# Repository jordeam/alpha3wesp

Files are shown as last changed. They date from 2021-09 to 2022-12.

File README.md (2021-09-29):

# alpha3wesp
Triphase trigger angle control using ESP32

## Pin connection

| ESP32 GPIO | Function |
|---|---|
| 15 | 60Hz square oscilator output for debug |
| 16 | 40kHz output oscilator for TPs |
| 17 | Gate of SCR 1 (Q1) |
| 18 | Gate of SCR 3 (Q3) |
| 19 | Gate of SCR 5 (Q5) |
| 25 | Gate of SCR 4 (Q4) |
| 26 | Gate of SCR 6 (Q6) |
| 27 | Gate of SCR 2 (Q2) |
| 4  | Grid Synchronism input |
| 36 | Analog input for alpha trigger angle |

The device works in 50Hz or 60Hz automatically.

SCR power bridge has its positive cycle devices tagged as Q1, for phase a, Q3 for phase b, and Q5 for phase c. The negative cycle for phase a is SCR number 4 (Q4), for phase b is Q6 and for phase c is Q2. This produces a trigger sequence in order, from Q1 to Q6.

## Circuit Example

An example of usage can be seen in [circuit-1](doc/example-circuit-1.pdf). In that circuit, a triphase full-bridge (or two way) rectifier is shown. Note the numbering of thyristors Q1 to Q6, it is very important to match with the ESP32 outputs. Also, certify that phases A, B and C are in the right sequence. For simplification, only one Gate Driver block is show, but it needs to be one for each thyristor.

An input of voltage from 0 to 2.5V means o to 180 degrees of trigger for each SCR.

## TODO

- accept inputs from UART, SPI, I2C, CAN and pulse width
- implement reversion capability for AC three-phase controllers
- use two phase synchronism signals to detect phase sequence order automatically
- as always, improve docs...

## Thanks

To all free software developers, thank you!

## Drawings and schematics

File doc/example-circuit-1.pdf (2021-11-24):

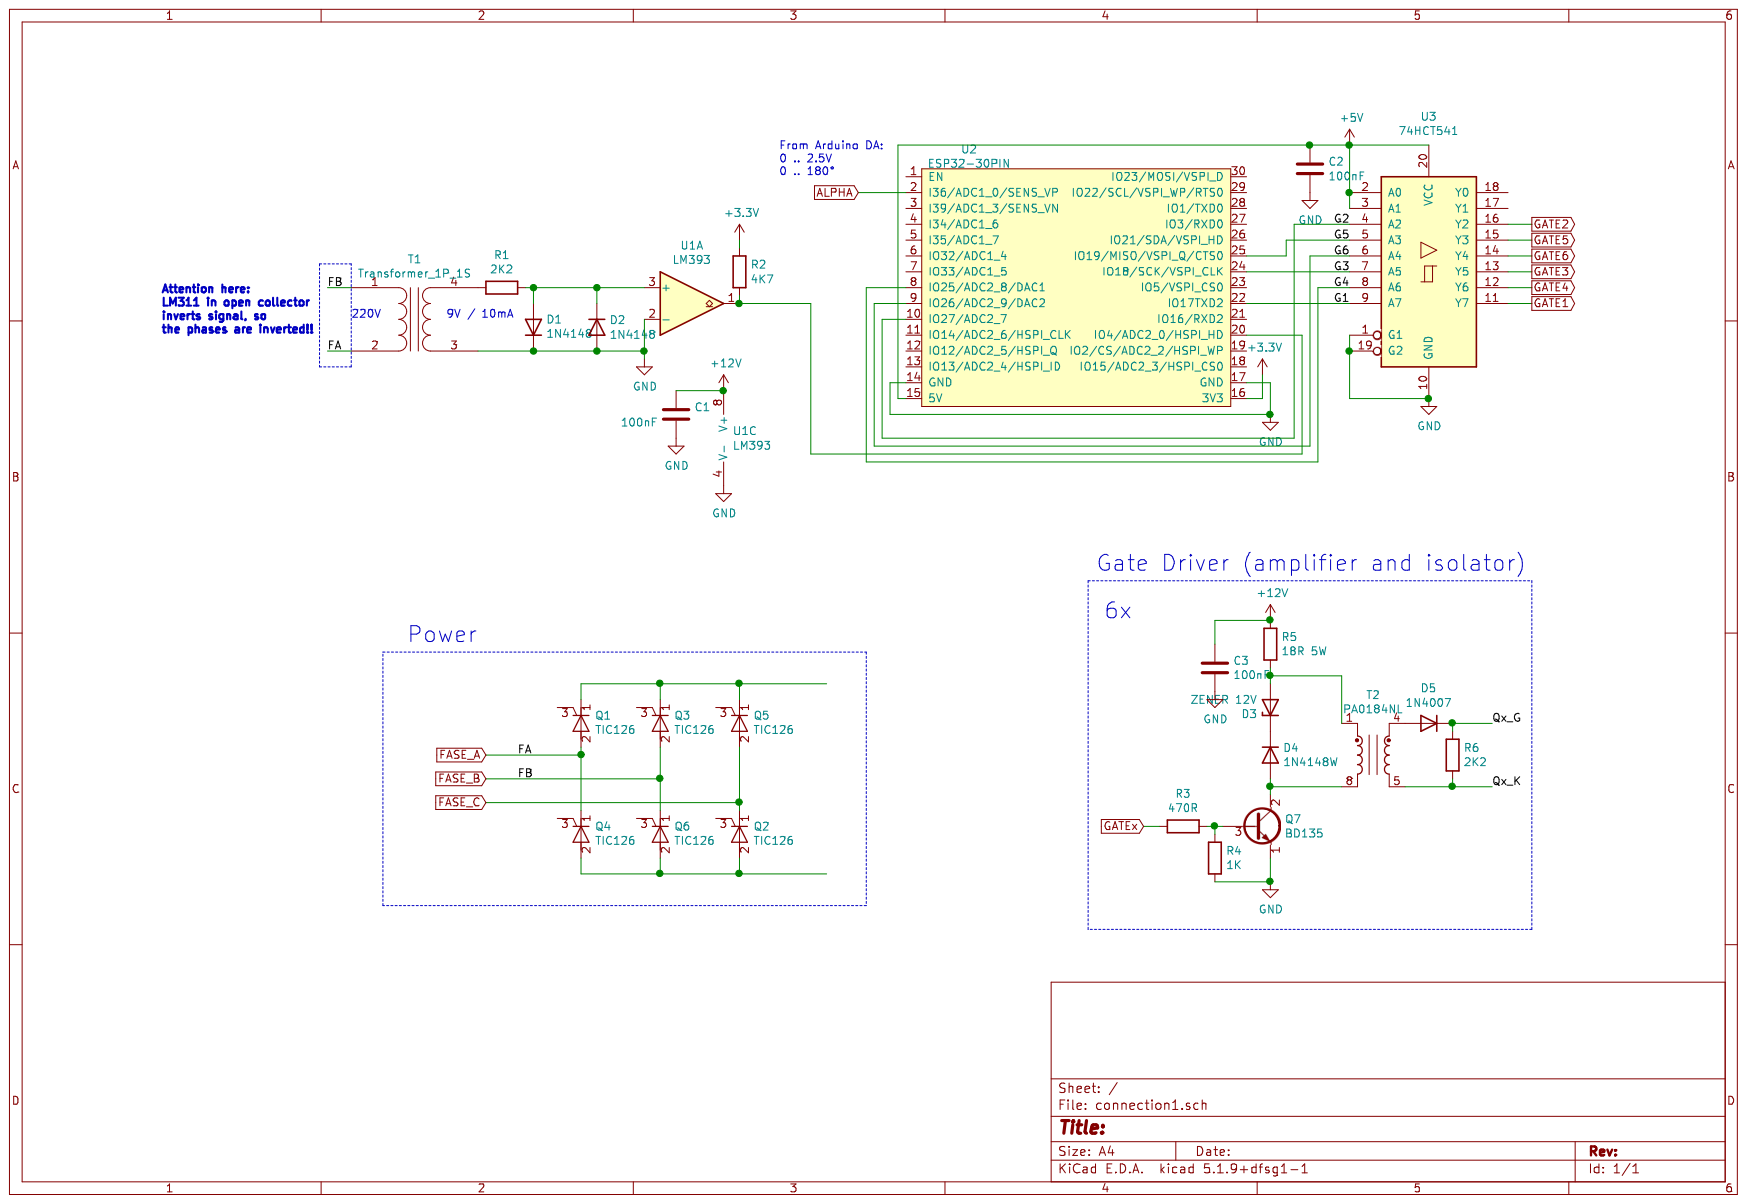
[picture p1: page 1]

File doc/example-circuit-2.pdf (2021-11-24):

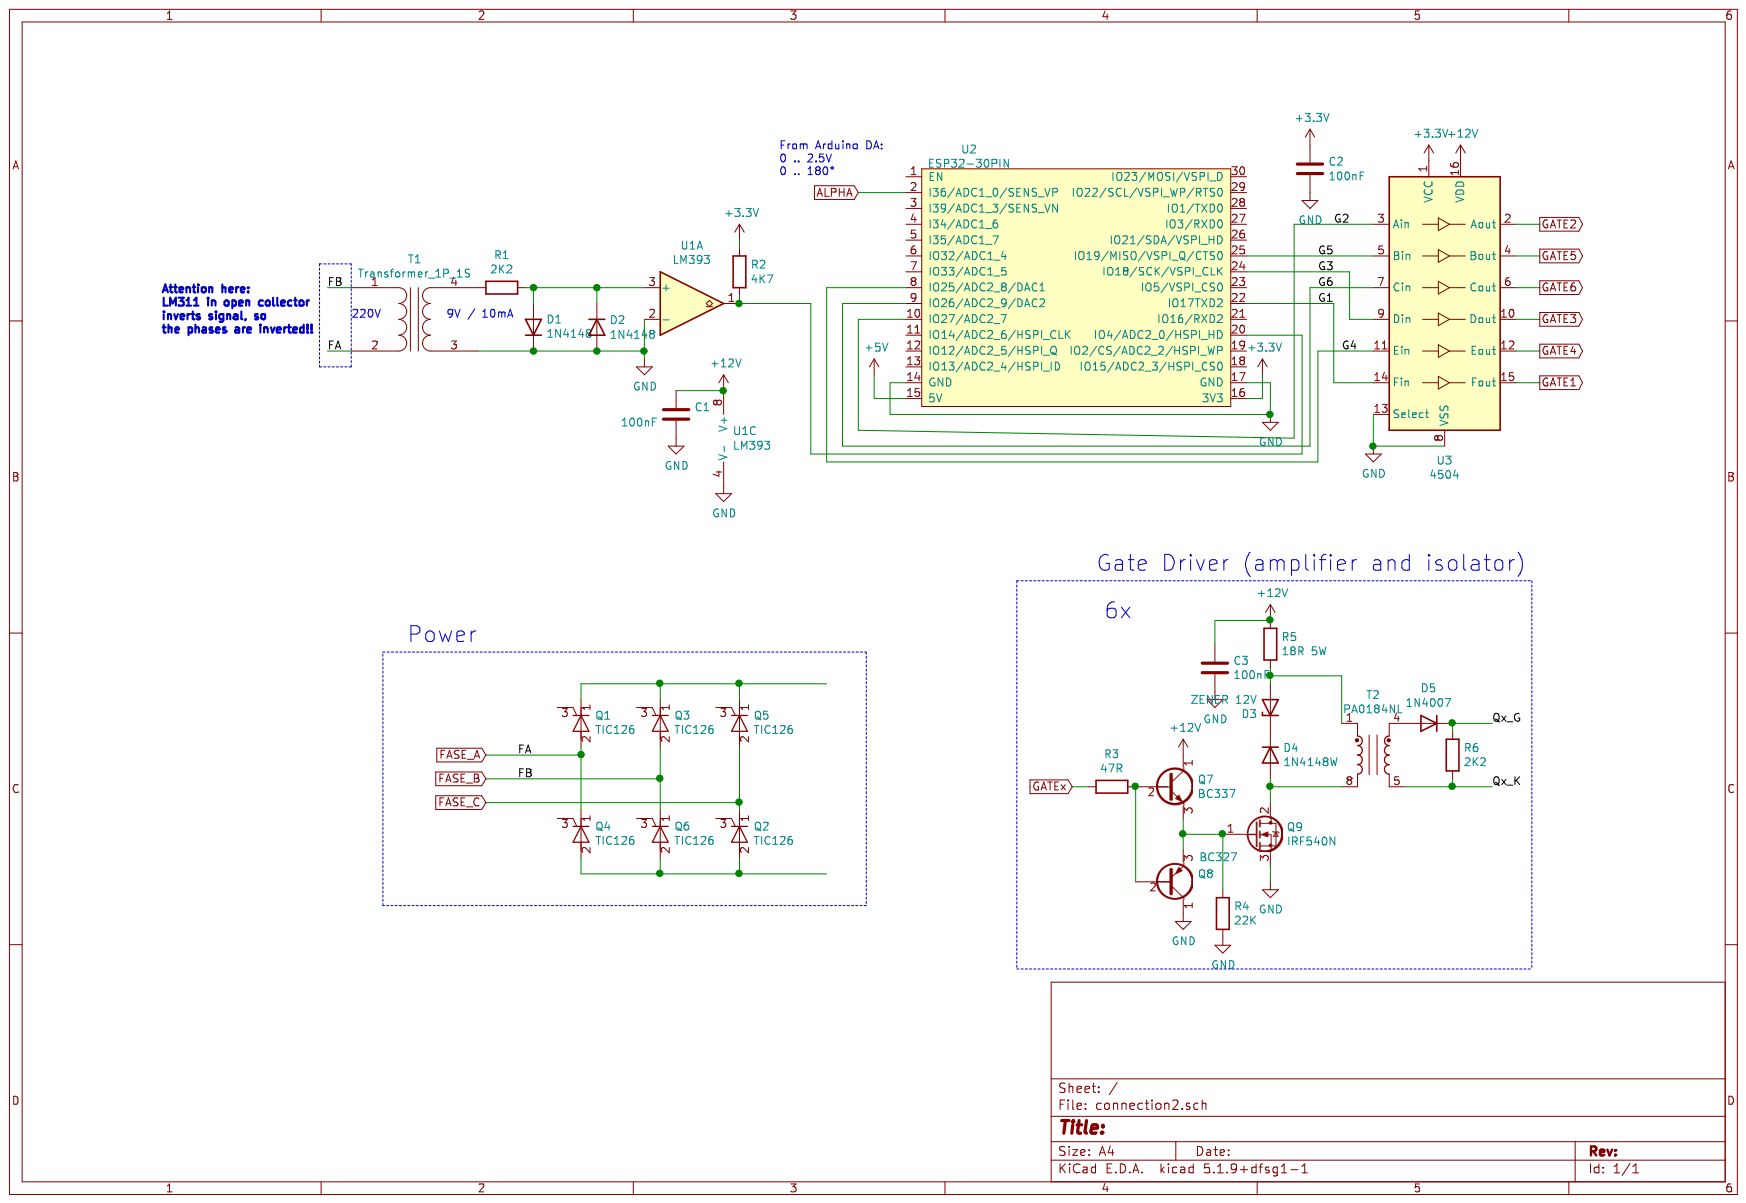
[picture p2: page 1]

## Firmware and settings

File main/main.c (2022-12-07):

#include <stddef.h>
#include <stdlib.h>
#include <stdint.h>
#include <string.h>

#include "freertos/FreeRTOS.h"
#include "freertos/task.h"
#include "freertos/queue.h"
#include "esp_intr_alloc.h"
#include "esp_attr.h"
#include "driver/timer.h"
#include "driver/gpio.h"
#include "driver/ledc.h"
#include "driver/adc.h"
#include "esp_adc_cal.h"

#include "pins.h"
#include "ledc_pwm.h"
#include "adc_mod.h"

#define GPIO_OUTPUT_PIN_SEL  (port_bit(LED_GPIO) | \
                              port_bit(SIGINT) | port_bit(SIGAD))

#define GPIO_INPUT_PIN_SEL  (port_bit(SYNC_GPIO) | port_bit(ADC_GPIO))

#define GATE_DUTY ((int)((1 << 10) * 0.4))

int sync;
int cnt, cnt_max = -1;
/* Maximum counter value used in last eval */
int cnt_max_e = 0;

/* the transitions */
struct tr {
  int rise[6], fall[6];
};

typedef struct tr tr_t;

tr_t gate;

static intr_handle_t s_timer_handle;
/* the alpha trigger angle in degrees */
float alpha = 60;

static void timer_isr(void* arg) {
  static int sync_old = 1;
  static tr_t g;

  gpio_set_level(SIGINT, 1);

  TIMERG0.int_clr_timers.t0 = 1;
  TIMERG0.hw_timer[0].config.alarm_en = 1;

  /* read SYNC */
  sync = gpio_get_level(SYNC_GPIO);

  if (sync && !sync_old && /* jitter ? */cnt > 20) {
    if (cnt_max < 0)
      cnt_max++;
    else if (cnt_max == 0)
      cnt_max = cnt;
    else {
      cnt_max += cnt;
      cnt_max >>= 1;
      memcpy(&g, &gate, sizeof(tr_t));

      /* Verify if Gates 4, 5 and 6 are higher than cnt */
      if (g.fall[3] >= cnt) {
        /* gpio_set_level(GATE4, 0); */
        ledc_set_duty(LEDC_HIGH_SPEED_MODE, LEDC_CHANNEL_4, 0);
        ledc_update_duty(LEDC_HIGH_SPEED_MODE, LEDC_CHANNEL_4);
      }
      if (g.fall[4] >= cnt) {
        /* gpio_set_level(GATE5, 0); */
        ledc_set_duty(LEDC_HIGH_SPEED_MODE, LEDC_CHANNEL_5, 0);
        ledc_update_duty(LEDC_HIGH_SPEED_MODE, LEDC_CHANNEL_5);
      }
      if (g.fall[5] >= cnt) {
        /* gpio_set_level(GATE6, 0); */
        ledc_set_duty(LEDC_HIGH_SPEED_MODE, LEDC_CHANNEL_6, 0);
        ledc_update_duty(LEDC_HIGH_SPEED_MODE, LEDC_CHANNEL_6);
      }
      if (g.rise[4] >= cnt) {
        /* gpio_set_level(GATE5, 1); */
        ledc_set_duty(LEDC_HIGH_SPEED_MODE, LEDC_CHANNEL_5, GATE_DUTY);
        ledc_update_duty(LEDC_HIGH_SPEED_MODE, LEDC_CHANNEL_5);
      }
      if (g.fall[3] >= cnt) {
        /* gpio_set_level(GATE4, 0); */
        ledc_set_duty(LEDC_HIGH_SPEED_MODE, LEDC_CHANNEL_4, 0);
        ledc_update_duty(LEDC_HIGH_SPEED_MODE, LEDC_CHANNEL_4);
      }
      if (g.rise[5] >= cnt) {
        /* gpio_set_level(GATE6, 1); */
        ledc_set_duty(LEDC_HIGH_SPEED_MODE, LEDC_CHANNEL_6, GATE_DUTY);
        ledc_update_duty(LEDC_HIGH_SPEED_MODE, LEDC_CHANNEL_6);
      }
    }
    cnt = 0;
  }

  /* do nothing if counter maximum is equal or less than zero*/
  if (cnt_max > 0) {
    /* refresh output pins */
    if (cnt == g.rise[0]) {
      /* gpio_set_level(GATE1, 1); */
      ledc_set_duty(LEDC_HIGH_SPEED_MODE, LEDC_CHANNEL_1, GATE_DUTY);
      ledc_update_duty(LEDC_HIGH_SPEED_MODE, LEDC_CHANNEL_1);
    }
    else if (cnt == g.fall[0]) {
      /* gpio_set_level(GATE1, 0); */
      ledc_set_duty(LEDC_HIGH_SPEED_MODE, LEDC_CHANNEL_1, 0);
      ledc_update_duty(LEDC_HIGH_SPEED_MODE, LEDC_CHANNEL_1);
    }
    if (cnt == g.rise[1]) {
      /* gpio_set_level(GATE2, 1); */
      ledc_set_duty(LEDC_HIGH_SPEED_MODE, LEDC_CHANNEL_2, GATE_DUTY);
      ledc_update_duty(LEDC_HIGH_SPEED_MODE, LEDC_CHANNEL_2);
    }
    else if (cnt == g.fall[1]) {
      /* gpio_set_level(GATE2, 0); */
      ledc_set_duty(LEDC_HIGH_SPEED_MODE, LEDC_CHANNEL_2, 0);
      ledc_update_duty(LEDC_HIGH_SPEED_MODE, LEDC_CHANNEL_2);
    }
    if (cnt == g.rise[2]) {
      /* gpio_set_level(GATE3, 1); */
      ledc_set_duty(LEDC_HIGH_SPEED_MODE, LEDC_CHANNEL_3, GATE_DUTY);
      ledc_update_duty(LEDC_HIGH_SPEED_MODE, LEDC_CHANNEL_3);
    }
    else if (cnt == g.fall[2]) {
      /* gpio_set_level(GATE3, 0); */
      ledc_set_duty(LEDC_HIGH_SPEED_MODE, LEDC_CHANNEL_3, 0);
      ledc_update_duty(LEDC_HIGH_SPEED_MODE, LEDC_CHANNEL_3);
    }
    if (cnt == g.rise[3]) {
      /* gpio_set_level(GATE4, 1); */
      ledc_set_duty(LEDC_HIGH_SPEED_MODE, LEDC_CHANNEL_4, GATE_DUTY);
      ledc_update_duty(LEDC_HIGH_SPEED_MODE, LEDC_CHANNEL_4);
    }
    else if (cnt == g.fall[3]) {
      /* gpio_set_level(GATE4, 0); */
      ledc_set_duty(LEDC_HIGH_SPEED_MODE, LEDC_CHANNEL_4, 0);
      ledc_update_duty(LEDC_HIGH_SPEED_MODE, LEDC_CHANNEL_4);
    }
    if (cnt == g.rise[4]) {
      /* gpio_set_level(GATE5, 1); */
      ledc_set_duty(LEDC_HIGH_SPEED_MODE, LEDC_CHANNEL_5, GATE_DUTY);
      ledc_update_duty(LEDC_HIGH_SPEED_MODE, LEDC_CHANNEL_5);
    }
    else if (cnt == g.fall[4]) {
      /* gpio_set_level(GATE5, 0); */
      ledc_set_duty(LEDC_HIGH_SPEED_MODE, LEDC_CHANNEL_5, 0);
      ledc_update_duty(LEDC_HIGH_SPEED_MODE, LEDC_CHANNEL_5);
    }
    if (cnt == g.rise[5]) {
      /* gpio_set_level(GATE6, 1); */
      ledc_set_duty(LEDC_HIGH_SPEED_MODE, LEDC_CHANNEL_6, GATE_DUTY);
      ledc_update_duty(LEDC_HIGH_SPEED_MODE, LEDC_CHANNEL_6);
    }
    else if (cnt == g.fall[5]) {
      /* gpio_set_level(GATE6, 0); */
      ledc_set_duty(LEDC_HIGH_SPEED_MODE, LEDC_CHANNEL_6, 0);
      ledc_update_duty(LEDC_HIGH_SPEED_MODE, LEDC_CHANNEL_6);
    }
  }

  /* increment counter */
  cnt++;
  /* refresh sync_old */
  sync_old = sync;
  /* flag interrupt exiting */
  gpio_set_level(SIGINT, 0);
}

void init_timer(int timer_period_us)
{
  timer_config_t timer_config = {
    .alarm_en = true,
    .counter_en = false,
    .intr_type = TIMER_INTR_LEVEL,
    .counter_dir = TIMER_COUNT_UP,
    .auto_reload = true,
    .divider = 80   /* 1 us per tick */
  };

  timer_init(TIMER_GROUP_0, TIMER_0, &timer_config);
  timer_set_counter_value(TIMER_GROUP_0, TIMER_0, 0);
  timer_set_alarm_value(TIMER_GROUP_0, TIMER_0, timer_period_us);
  timer_enable_intr(TIMER_GROUP_0, TIMER_0);
  timer_isr_register(TIMER_GROUP_0, TIMER_0, &timer_isr, NULL, 0, &s_timer_handle);

  timer_start(TIMER_GROUP_0, TIMER_0);
}

/* task to eval all trigger event times */
void eval_triggers(void * pvParams) {
  for (;;) {
    gpio_set_level(SIGAD, 1);
    int val = adc1_get_raw(ADC1_CHANNEL_0);
    gpio_set_level(SIGAD, 0);

    alpha = 180.0f * val / (1 << 12);
    cnt_max_e = cnt_max;
    /* verify if it detected the first sync pulse */
    if (cnt_max_e != 0) {
      if (alpha > 180.0f)
        alpha = 180.0f;
      float alpha_n = alpha / 360.0;
      gate.rise[0] = cnt_max_e * alpha_n;
      gate.fall[0] = cnt_max_e * 0.5;
      gate.rise[1] = cnt_max_e * (alpha_n + 0.1666);
      gate.fall[1] = cnt_max_e * 0.6666;
      gate.rise[2] = cnt_max_e * (alpha_n + 0.3333);
      gate.fall[2] = cnt_max_e * 0.8333;
      gate.rise[3] = cnt_max_e * (alpha_n + 0.5);
      gate.fall[3] = cnt_max_e - 1;
      gate.rise[4] = cnt_max_e * (alpha_n + 0.6666);
      if (gate.rise[4] >= cnt_max_e)
        gate.rise[4] -= cnt_max_e;
      gate.fall[4] = cnt_max_e * 0.1666;
      gate.rise[5] = cnt_max_e * (alpha_n + 0.8333);
      if (gate.rise[5] >= cnt_max_e)
        gate.rise[5] -= cnt_max_e;
      gate.fall[5] = cnt_max_e * 0.3333;
    }

    /* wait for something ? */
    vTaskDelay(pdMS_TO_TICKS(20));
  }
}

void led_task(void * pvParams) {
  for (int cnt = 0;;cnt = !cnt) {
    vTaskDelay(pdMS_TO_TICKS(200));
    gpio_set_level(LED_GPIO, cnt % 2);
  }
}

void app_main()
{
  /* init GPIOs */
  gpio_config_t io_conf_o = {
    .intr_type = GPIO_INTR_DISABLE,
    .mode = GPIO_MODE_OUTPUT,
    .pin_bit_mask = GPIO_OUTPUT_PIN_SEL,
    .pull_down_en = 0,
    .pull_up_en = 0
  };
  //configure GPIO with the given settings
  gpio_config(&io_conf_o);

  gpio_config_t io_conf_i = {
    .intr_type = GPIO_INTR_DISABLE,
    .pin_bit_mask = GPIO_INPUT_PIN_SEL,
    .mode = GPIO_MODE_INPUT,
    .pull_up_en = 0,
    .pull_down_en = 0,
  };
  gpio_config(&io_conf_i);

  /* configure LED PWMs */
  ledc_pwm_config();

  /* configure ADC raw */
  adc_config();

  /* register 50us interrupt SR */
  init_timer(50);

  /* TODO: clear this */
  /* alpha for test purposes */

  xTaskCreate(led_task, "led_task", 4096, NULL, 5, NULL);
  xTaskCreate(eval_triggers, "eval_triggers", 4096, NULL, 4, NULL);
}

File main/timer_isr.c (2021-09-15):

#include <stddef.h>
#include <stdlib.h>
#include <stdint.h>
#include "freertos/FreeRTOS.h"
#include "freertos/task.h"
#include "freertos/queue.h"
#include "esp_intr_alloc.h"
#include "esp_attr.h"
#include "driver/timer.h"
#include "driver/gpio.h"

/* Outputs:
   GPIO2: internal LED
   GPIO16: Oscilator 40kHz,
   GPIO17, 18, 19: positive semicycle phases 1, 2 and 3,
   GPIO25, 26, 27: negative senicycle phases 1, 2 and 3 */
#define GPIO_OUTPUT_PIN_SEL  ((1ULL<<2) | (1ULL<<16) | (1ULL<<17) | (1ULL<<18) | (1ULL<<19) | (1ULL<<25) | (1ULL<<26) | (1ULL<<27))

/* Inputs:
   GPIO4: sync
   GPIO34: ADC input angle
 */
#define GPIO_INPUT_PIN_SEL  ((1ULL<<4) | (1ULL<<34))

int sync;
uint32_t cnt, cnt_max = 0;
static intr_handle_t s_timer_handle;

static void timer_isr(void* arg)
{
  static int sync_old = 1;
  TIMERG0.int_clr_timers.t0 = 1;
  TIMERG0.hw_timer[0].config.alarm_en = 1;

  /* read SYNC */
  sync = gpio_get_level(4);

  if (sync && !sync_old) {
    cnt_max = cnt;
    cnt = 0;
  }
  else
    cnt++;
  sync_old = sync;

  /* eval outputs */
  /* refresh output pins */
}

void init_timer(int timer_period_us)
{
  timer_config_t config = {
    .alarm_en = true,
    .counter_en = false,
    .intr_type = TIMER_INTR_LEVEL,
    .counter_dir = TIMER_COUNT_UP,
    .auto_reload = true,
    .divider = 80   /* 1 us per tick */
  };

  timer_init(TIMER_GROUP_0, TIMER_0, &config);
  timer_set_counter_value(TIMER_GROUP_0, TIMER_0, 0);
  timer_set_alarm_value(TIMER_GROUP_0, TIMER_0, timer_period_us);
  timer_enable_intr(TIMER_GROUP_0, TIMER_0);
  timer_isr_register(TIMER_GROUP_0, TIMER_0, &timer_isr, NULL, 0, &s_timer_handle);

  timer_start(TIMER_GROUP_0, TIMER_0);
}

void app_main()
{
  /* init GPIOs */
  gpio_config_t io_conf = {
    .intr_type = GPIO_INTR_DISABLE,
    .mode = GPIO_MODE_OUTPUT,
    .pin_bit_mask = GPIO_OUTPUT_PIN_SEL,
    .pull_down_en = 0,
    .pull_up_en = 0
  };
  //configure GPIO with the given settings
  gpio_config(&io_conf);

  io_conf.intr_type = GPIO_INTR_DISABLE;
  io_conf.pin_bit_mask = GPIO_INPUT_PIN_SEL;
  io_conf.mode = GPIO_MODE_INPUT;
  io_conf.pull_up_en = 0;
  io_conf.pull_down_en = 0;
  gpio_config(&io_conf);


  init_timer(50);

  int cnt = 0;
  for (;;cnt = !cnt) {
    vTaskDelay(200 / portTICK_RATE_MS);
    gpio_set_level(2, cnt % 2);
  }
}

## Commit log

2021-09-16 Adding ADC support and oscilators
2021-09-22 First functional revision
    TODO: input alpha value from ADC or any kind of serial, as UART or CAN.
2021-09-29 Adding a circuit example
2021-09-29 Improving docs, adding an example circuit
2021-09-29 Adding Kicad example circuit
    [connection1.sch]
2021-09-29 Improving docs...
    [connection1.sch]
2021-09-29 Inserting code to analog input on pin 36 (ADC channel 0)
2021-09-29 Updating synchronism polarity
    [connection1.sch]
2021-10-06 Zener diode polarity in demagnetization circuit
    [connection1.sch]
2021-10-20 Bugs, bugs and bugs...
    [ledc_pwm.c, main.c]
2021-11-17 Using LM393 instead of LM311
    [connection1.sch]
2022-10-05 Updating to Kicad version 6
    [connection1.kicad_sch, connection1.sch, connection2.kicad_sch]
2022-10-05 Deleting old file format
    [connection2.sch]
2022-12-07 Adapting to new version of board
